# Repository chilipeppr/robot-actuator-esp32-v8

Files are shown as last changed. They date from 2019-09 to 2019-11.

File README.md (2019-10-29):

# robot-actuator-esp32-v8
This is the repo for the robot actuator v8 based on an ESP32 as the brains of each robot arm actuator.

This repository contains the latest design for the small actuator including:
- PCB schematic and board file (Eagle)
- Bill of Materials
- Fusion 360 files
- STL files for 3D printing
- NodeMCU ESP32 for Lua firmware with touch module, pulse counter module, RMT TX module, and gpiomatrix module.
- Lua code for actuator
- Link to ChiliPeppr http://chilipeppr.com/arm workspace to control the actuator and to ChiliPeppr ESP32 for Lua workspace for uploading code to the ESP32 device http://chilipeppr.com/esp32
- Heat management test results
- Youtube videos

This actuator is based on the amazing design of Jeff Kerr's (LoboCNC on Thingiverse) 3D printed robot arm WE-R2.4 six axis robot arm. https://www.thingiverse.com/thing:3327968

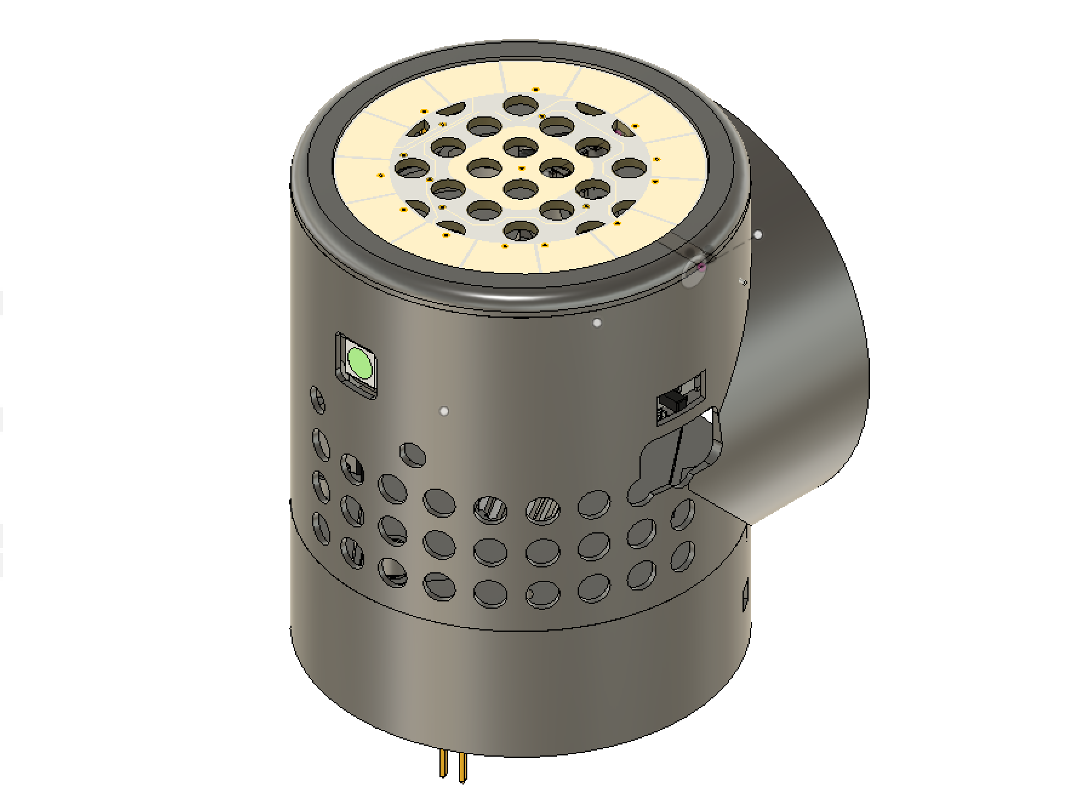
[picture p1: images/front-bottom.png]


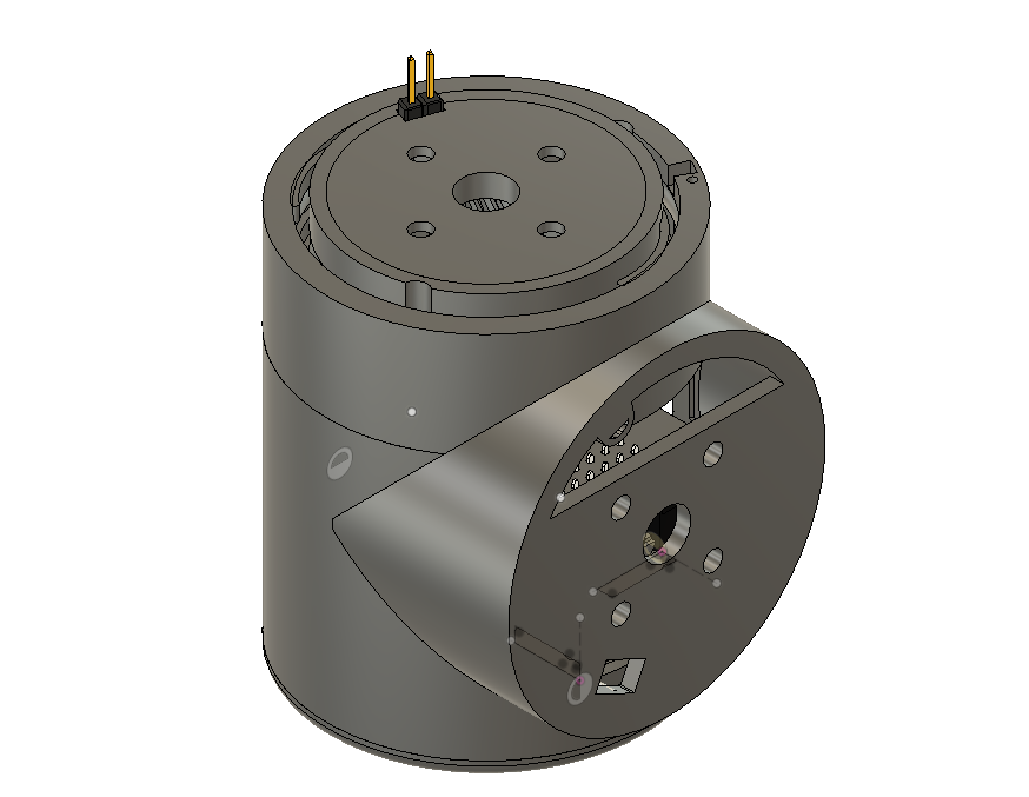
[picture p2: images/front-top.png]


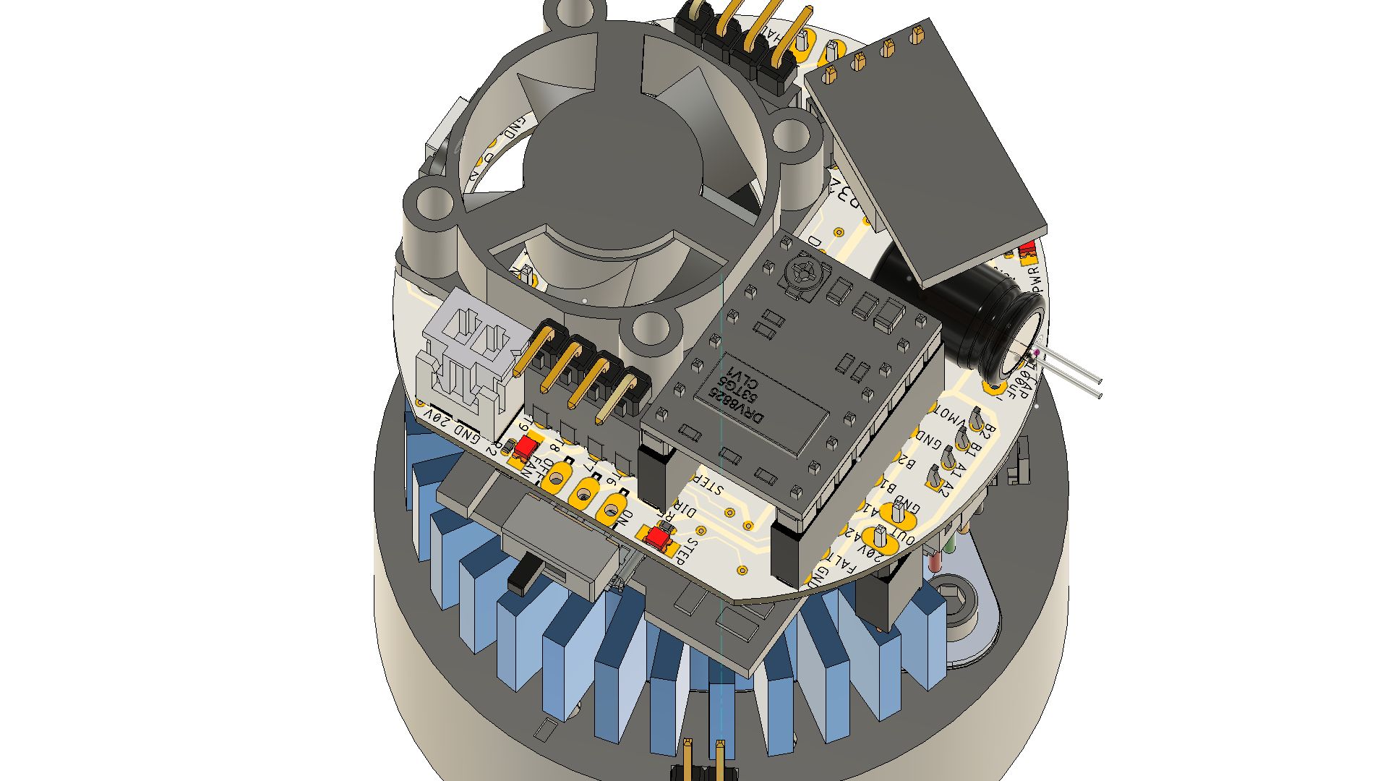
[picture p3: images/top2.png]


# Eagle Files

The main PCB board in Eagle.
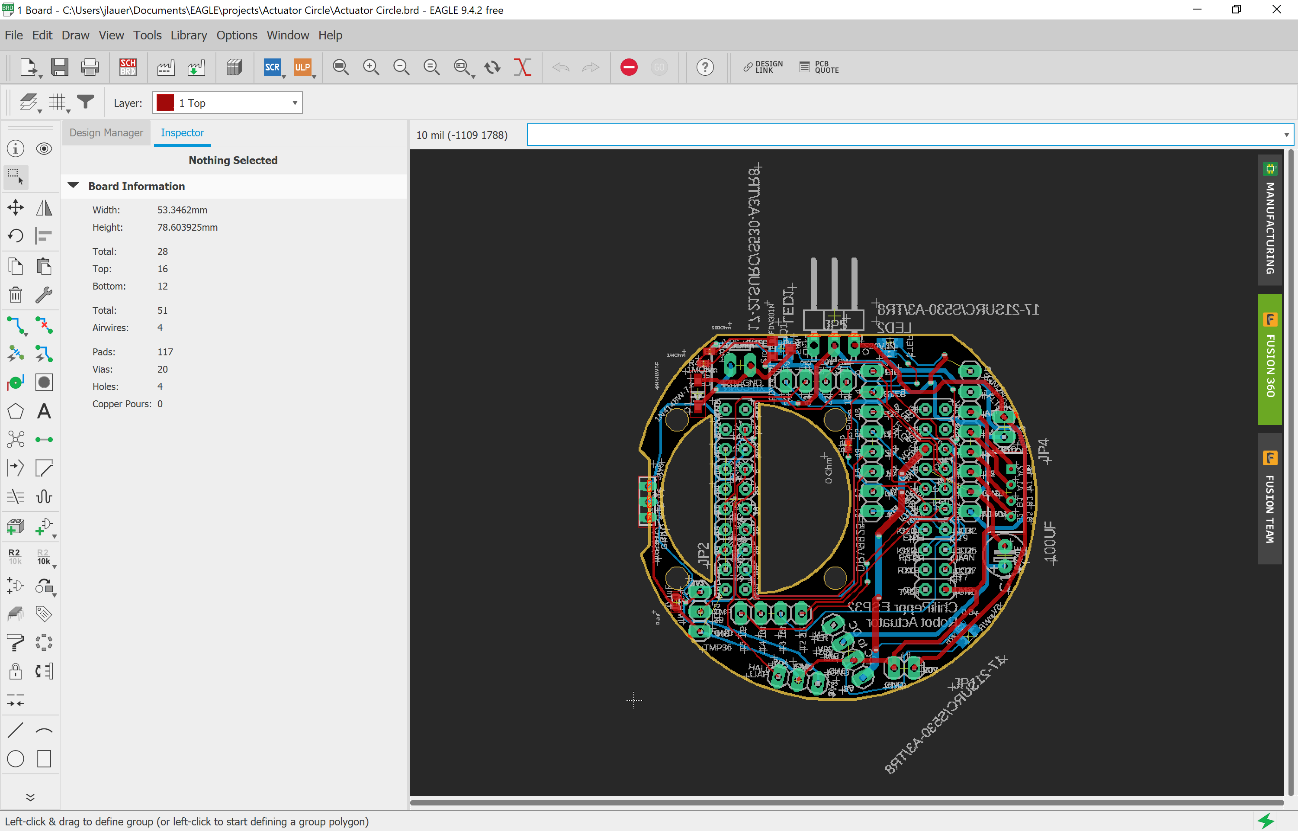
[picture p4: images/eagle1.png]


Top
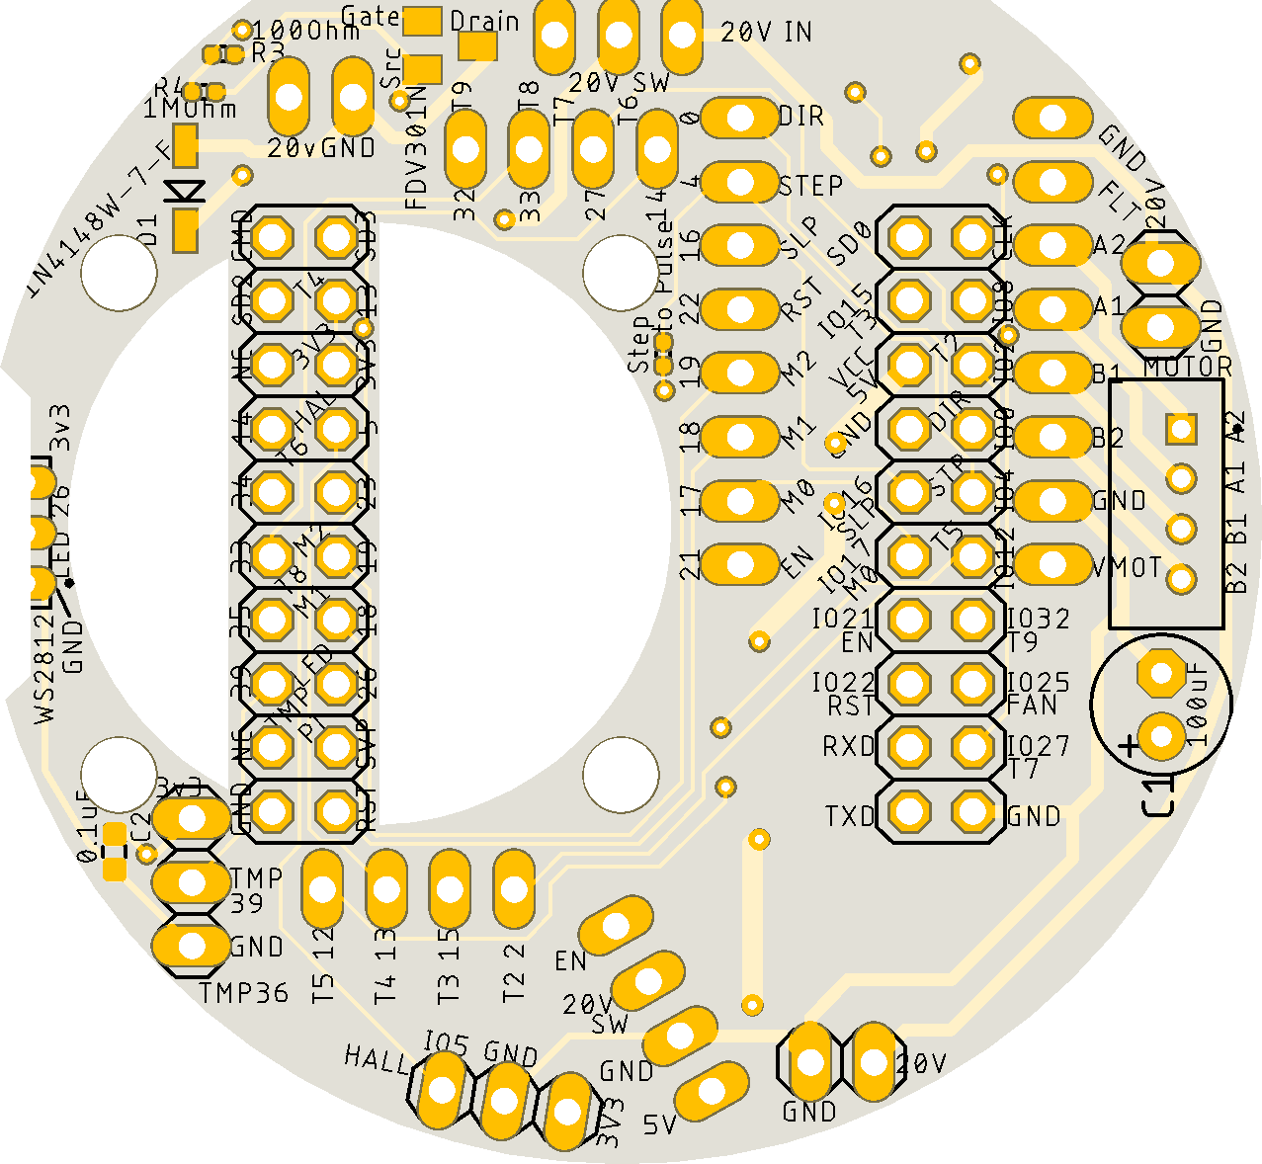
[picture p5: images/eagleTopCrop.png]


Bottom
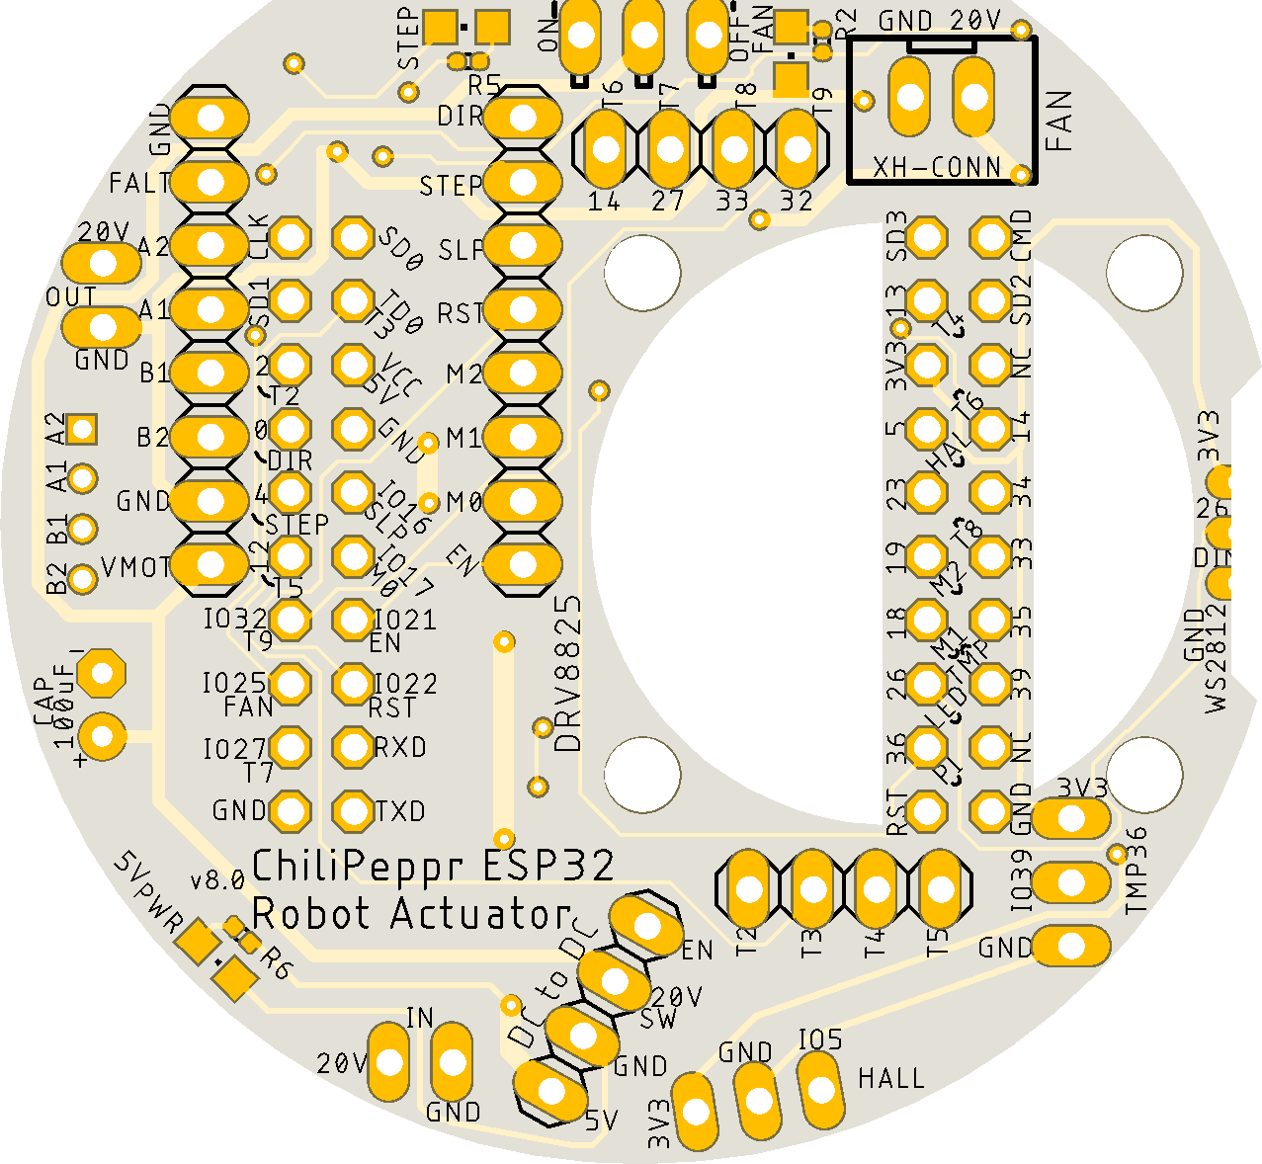
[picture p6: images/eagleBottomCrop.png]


The touch PCB board in Eagle.
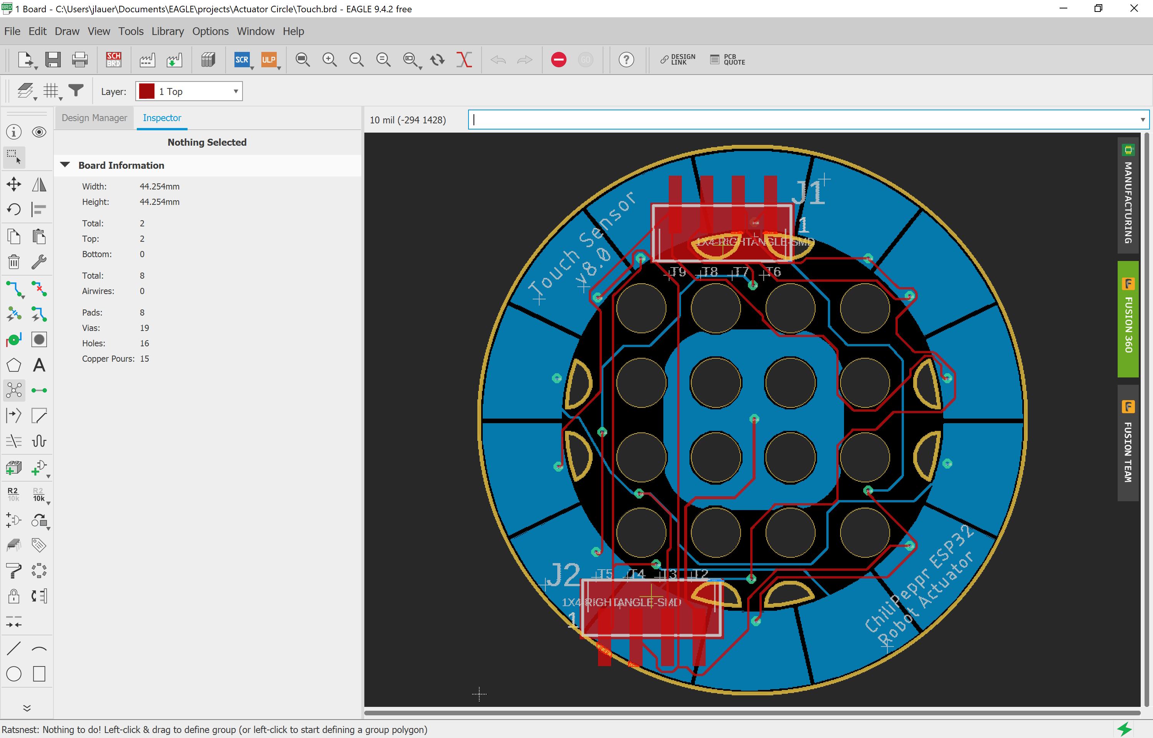
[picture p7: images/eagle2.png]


# Ordering PCBs

When ordering PCBs, keep in mind the thickness of the main PCB is 1.0 mm while the touch PCB is 1.2 mm. A white soldermask is recommended, but not important.

Main PCB is 1.0 mm thickness
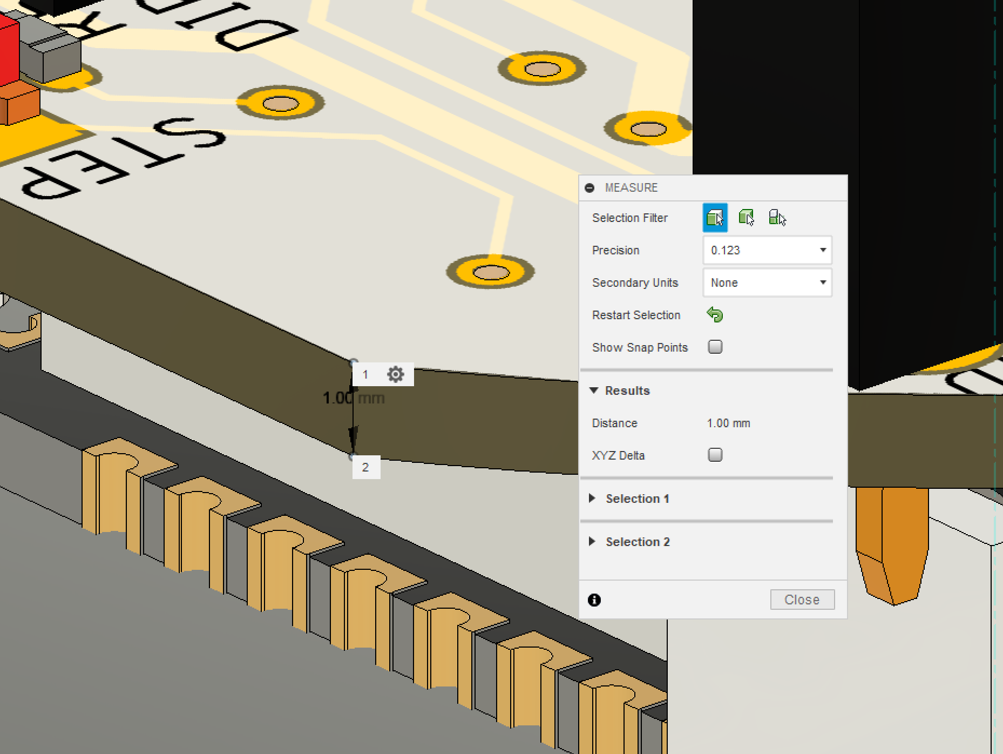
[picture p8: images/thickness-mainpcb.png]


Touch PCB is 1.2 mm thickness
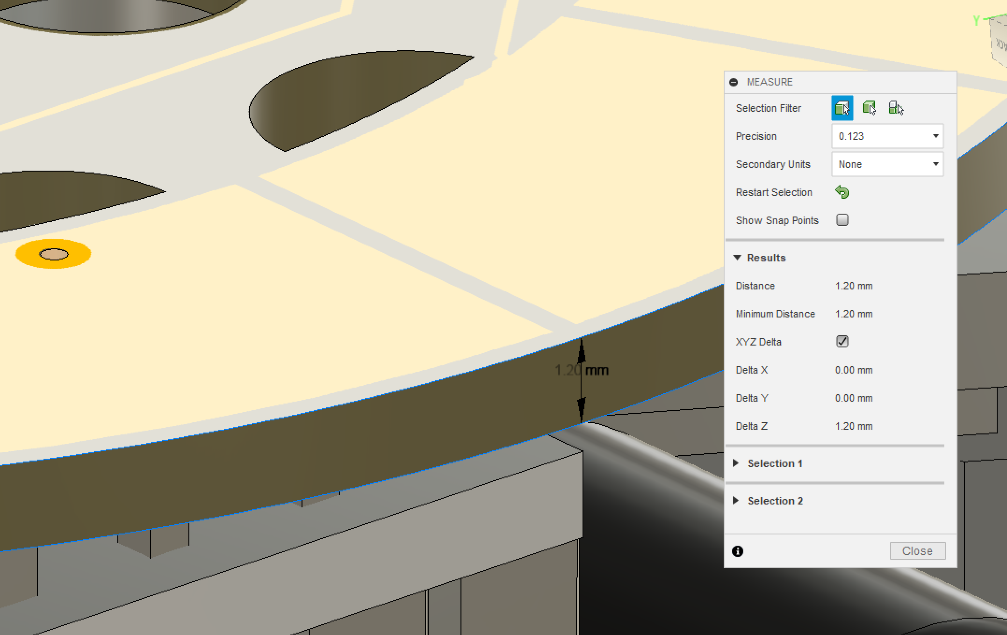
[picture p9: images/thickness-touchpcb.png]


# Fusion 360

The CAD files in Fusion360.
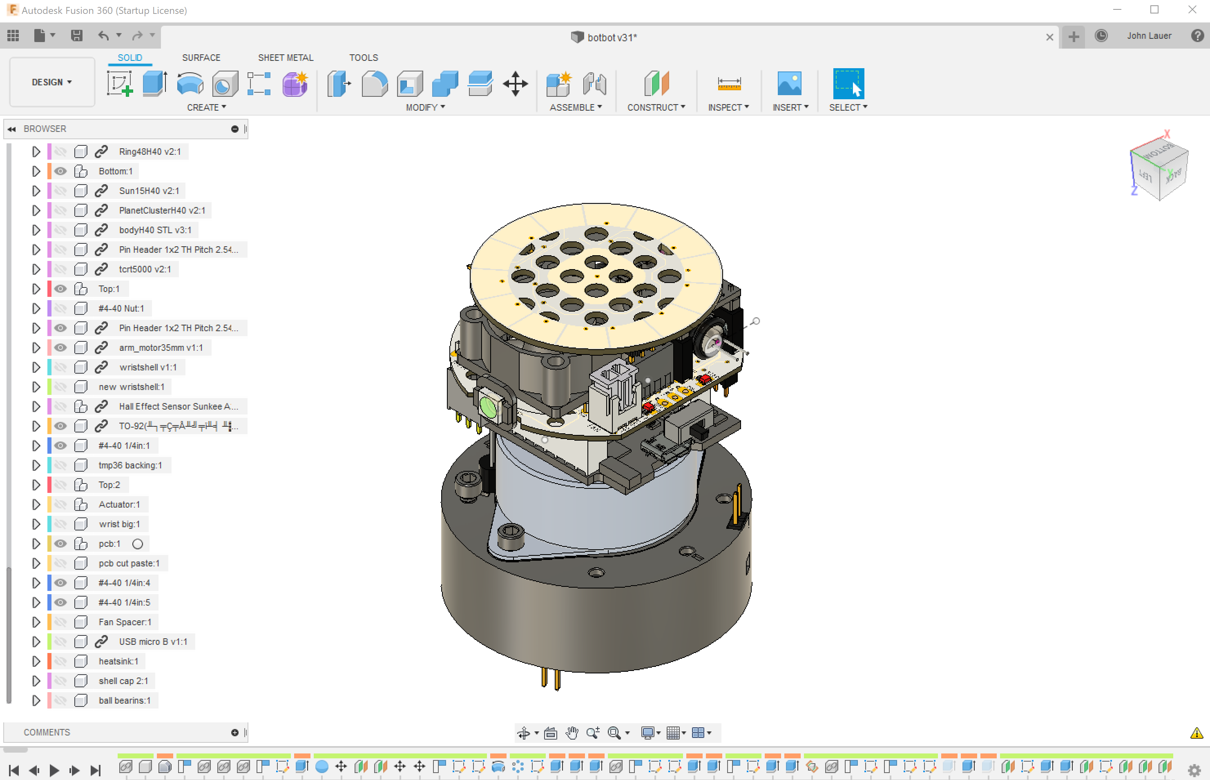
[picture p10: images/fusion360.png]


# ChiliPeppr

ChiliPeppr Robot Arm Workspace (Work in progress)
http://chilipeppr.com/arm

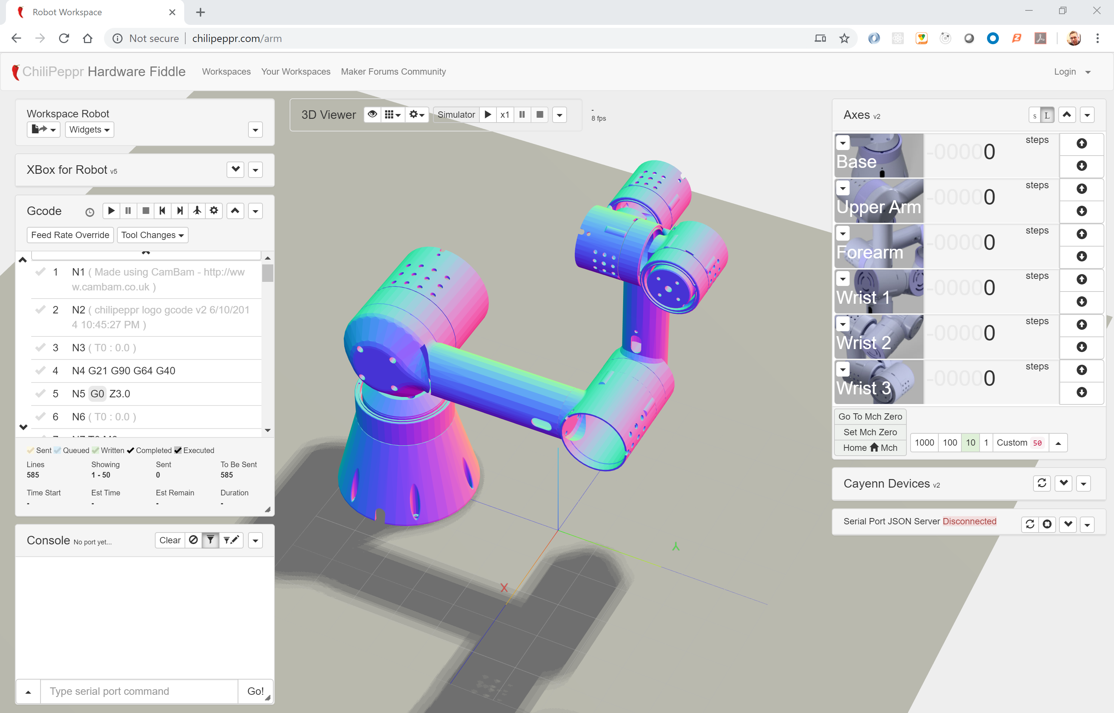
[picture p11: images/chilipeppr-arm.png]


ChiliPeppr ESP32 for Lua Workspace for editing/uploading code
http://chilipeppr.com/esp32

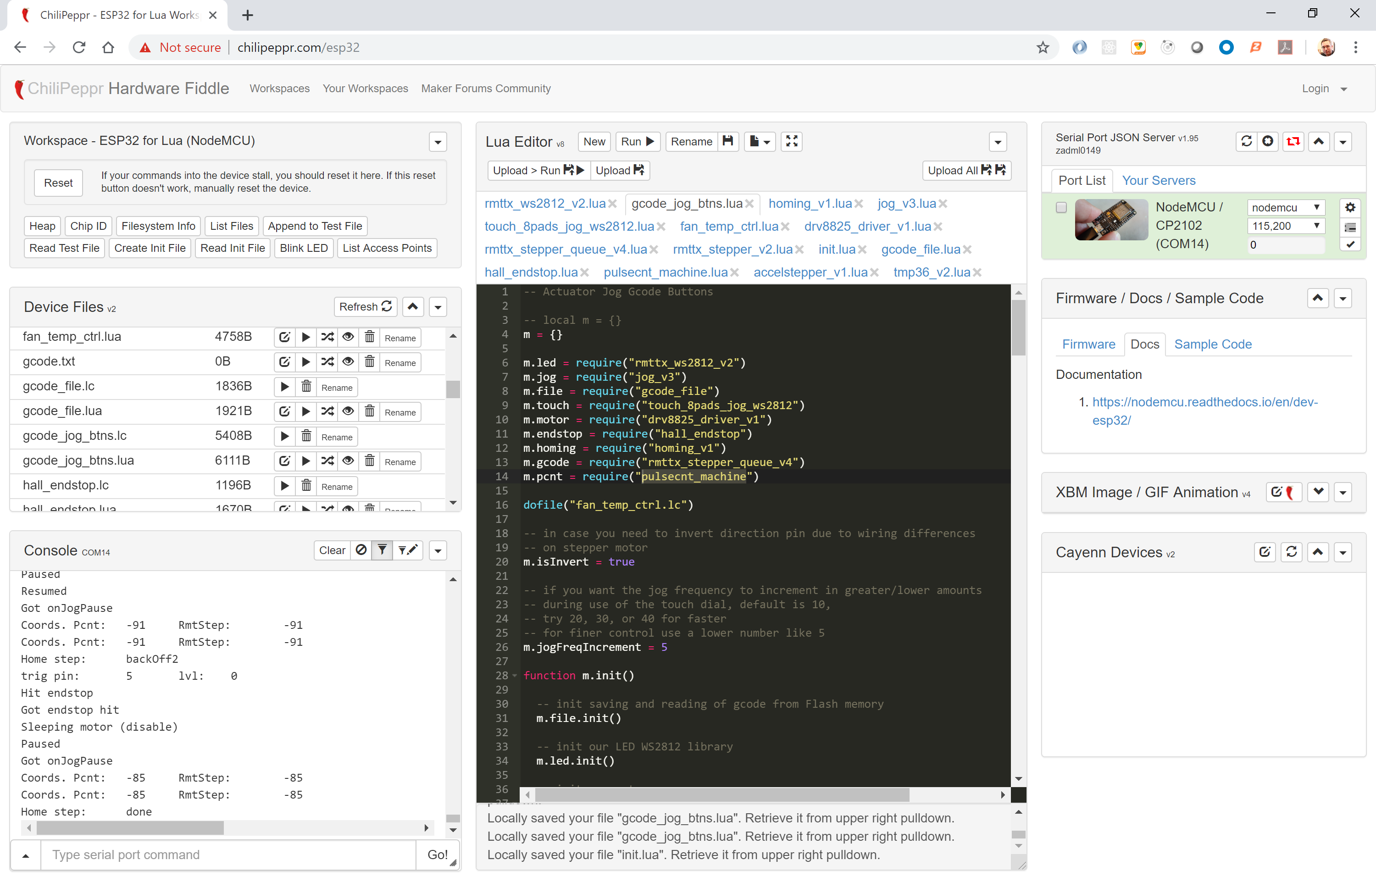
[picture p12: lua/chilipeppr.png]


# Heat Test

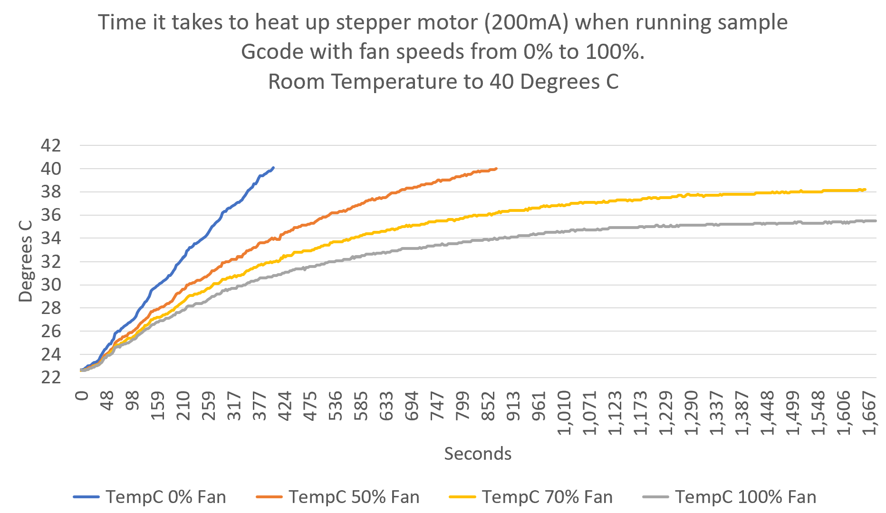
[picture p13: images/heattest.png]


# Youtube Videos

Part 1
https://www.youtube.com/watch?v=tEbJV32GyYU



Part 2
https://www.youtube.com/watch?v=RdmdFIhCo4M



Part 3
https://youtu.be/4o3d7_WZ_DQ



<!-- # Pins Used on ESP32

|GPIO|Used|Input|Output|Notes|
|----|-----|---|-----|
|0|Yes|Yes|Yes|motor.pinDir|
|1|TX pin|OK|debug output at boot|
|2|OK|OK|connected to on-board LED|
|3|OK|RX pin|HIGH at boot|
|4|OK|OK|
|5|OK|OK|outputs PWM signal at boot|
|6|x|x|connected to the integrated SPI flash|
|7|x|x|connected to the integrated SPI flash|
|8|x|x|connected to the integrated SPI flash|
|9|x|x|connected to the integrated SPI flash|
|10|x|x|connected to the integrated SPI flash|
|11|x|x|connected to the integrated SPI flash|
|12|OK|OK|boot fail if pulled high|
|13|OK|OK|
|14|OK|OK|outputs PWM signal at boot|
|15|OK|OK|outputs PWM signal at boot|
|16|OK|OK|
|17|OK|OK|
|18|OK|OK|
|19|OK|OK|
|21|OK|OK|
|22|OK|OK|
|23|OK|OK|
|25|OK|OK|
|26|OK|OK|
|27|OK|OK|
|32|OK|OK|
|33|OK|OK|
|34|OK|input only|
|35|OK|input only|
|36|OK|input only|
|39|OK|input only| -->

# Bill of Materials

| Ref | Part |  Price |  Quantity  |  Ext Price  | URL | Notes |
|---|---|---|---|---|---|---|
| | | | | | | |
| | PCB | | |  $- | | |
| | ESP32 Wemos Mini |  $4.05 |  1 |  $4.05 | https://www.aliexpress.com/item/32839344778.html | |
| | 2x10 Pin Header Female for ESP32 |  $0.12 |  2 |  $0.24 | https://lcsc.com/product-detail/Pin-Header-Female-Header_Boom-Precision-Elec-2-54mm-2-10-Straight-Female-header_C30867.html | Solder to the ESP32 board |
| C1 | 2x10 Pin Header Male for ESP32 |  $0.10 |  1 |  $0.10 | https://lcsc.com/product-detail/Pin-Header-Female-Header_Shenzhen-Cankemeng-Headers-Pins-2-10P-2-54mm-Straight-line_C124359.html | Solder to main PCB |
| | DRV8825 |  $0.88 |  1 |  $0.88 | https://www.aliexpress.com/item/33010878323.html | The most popular stepper driver out there. Simple and easy. |
| | 100uF 50V Capacitor for DRV8825 |  $0.13 |  1 |  $0.13 | https://lcsc.com/product-detail/Aluminum-Electrolytic-Capacitors-Leaded_PANASONIC-EEUFM1H101_C128473.html | The big capacitor for stepper motor driver |
| | DC to DC 24V to 5V Converter |  $0.48 |  1 |  $0.48 | https://www.aliexpress.com/item/32796268715.html | Little board from Aliexpress to get us to 5V on the cheap |
| | Fan 25mm 12V |  $1.08 |  1 |  $1.08 | https://www.aliexpress.com/item/33026177502.html | Silent fan that we overdrive to 20v for brief periods if heat spikes, otherwise we leave it off |
| R3 | Fan Mosfet FDV301N 25V 220mA SOT-23 |  $0.04 |  1 |  $0.04 | https://lcsc.com/product-detail/MOSFET_ON-Semicon_FDV301N_ON-Semicon-ON-FDV301N_C15310.html | Allows PWM speed control of fan. Run around 20Hz. |
| R4 | Fan Diode Protector 100V 300mA SOD-123 |  $0.02 |  1 |  $0.02 | https://lcsc.com/product-detail/Switching-Diode_DIODES_1N4148W-7-F_1N4148W-7-F_C83528.html | When fan switches off from Mosfet, it generates back current, so this diode lets it loop back into the fan to get absorbed |
| | Fan 100Ohm gate resistor 0402 |  $0.01 |  1 |  $0.01 | https://lcsc.com/product-detail/Chip-Resistor-Surface-Mount_100R-100R-1_C106232.html | Absorbs feedback attenuation |
| | Fan 1MOhm pull-down resistor 0402 |  $0.01 |  1 |  $0.01 | https://lcsc.com/product-detail/Chip-Resistor-Surface-Mount_1MR-105-5_C144054.html | Pulldown resistor to ground to shut off mosfet |
| | JST XH Male Connector for fan |  $0.04 |  1 |  $0.04 | https://lcsc.com/product-detail/Wire-To-Board-Wire-To-Wire-Connector_JST-Sales-America_B2B-XH-A-LF-SN_JST-Sales-America-B2B-XH-A-LF-SN_C158012.html | |
| | JST XH Crimp Connector for fan wire |  $0.01 |  2 |  $0.02 | https://lcsc.com/product-detail/New-Arrivals_JST-Sales-America-SXH-001T-P0-6N_C385122.html | In case you have to reterminate the fan wire, get these crimp connectors. You need a crimp tool. |
| | JST XH Female Connector for fan wire |  $0.02 |  1 |  $0.02 | https://lcsc.com/product-detail/Rectangular-Connectors-Housings_JST-Sales-America_XHP-2_JST-Sales-America-XHP-2_C144401.html | In case you have to reterminate the fan wire, get this female housing to slide the crimp connectors into |
| | WS2812B White |  $0.15 |  1 |  $0.15 | https://www.aliexpress.com/item/32960205936.html | Break off one LED and solder to side of PCB at 90 degree angle. Connect center pin to DIN, not DOUT. |
| | Red LED 0805 |  $0.02 |  3 |  $0.06 | https://lcsc.com/product-detail/Light-Emitting-Diodes-LED_0805-Red-LED-Iv-61mcd-Typ-atIF-20mA_C72037.html | Indicator LEDs |
| R5, R2 | 1KOhm current limit resistor for LED 0402 |  $0.01 |  2 |  $0.02 | https://lcsc.com/product-detail/Chip-Resistor-Surface-Mount_1KR-1001-1_C106235.html | The LEDs on the 3.3v bus for step and fan indicator use 1K to give LED about 1ma of current so it lights up very dim, but enough to indicate status. |
| R6 | 2KOhm current limit resistor for power LED 0402 |  $0.01 |  1 |  $0.01 | https://lcsc.com/product-detail/Chip-Resistor-Surface-Mount_Uniroyal-Elec-0402WGF2001TCE_C4109.html | The power LED is on a 5v bus. 2K gives it about 1.5ma of current for a dim indicator. |
| | 8 Pin Female Header 2.54mm |  $0.14 |  2 |  $0.28 | https://lcsc.com/product-detail/Pin-Header-Female-Header_Changjiang-Connectors-A2541HWV-8P_C225505.html | 2 needed for DRV8825 connection to main PCB. |
| | 4 Pin Female Header 2.54mm |  $0.07 |  3 |  $0.22 | https://lcsc.com/product-detail/Pin-Header-Female-Header_Shenzhen-Cankemeng-Female-header-1-4P-2-54mm-Straight-line_C124413.html | 1 for DC to DC, 2 for touch sensor PCB connection |
| | 3 Pin Female Header 2.54mm |  $0.06 |  2 |  $0.11 | https://lcsc.com/product-detail/Pin-Header-Female-Header_Shenzhen-Cankemeng-22025403P00CKMT_C146690.html | One for Hall sensor, one for TMP36. |
| | 2 Pin Female Header 2.54mm |  $0.03 |  4 |  $0.10 | https://lcsc.com/product-detail/Pin-Header-Female-Header_Boom-Precision-Elec-2-54-1-2PFemale_C49661.html | 2 for incoming 20v from slip ring. 2 for outgoing 20v to slip ring. |
| | JST PH B4B-K-S Male Header for Stepper |  $0.17 |  1 |  $0.17 | https://lcsc.com/product-detail/Wire-To-Board-Wire-To-Wire-Connector_JST-Sales-America_B4B-PH-K-LF-SN_JST-Sales-America-B4B-PH-K-LF-SN_C265289.html | Socket soldered to PCB |
| | JST PHR-4 Female Header for Stepper Cable |  $0.02 |  1 |  $0.02 | https://lcsc.com/product-detail/Connectors_JST_PHR-4_PHR-4-4P-pitch2-0mm-Plastic-shell_C111514.html | End of wire crimped connector |
| C2 | JST SPH Crimp Connector |  $0.01 |  4 |  $0.03 | https://lcsc.com/product-detail/Rectangular-Connectors-Contacts_JST_SPH-002T-P0-5S_SPH-002T-P0-5S-PH-T-PH-2-0_C111515.html | Individual crimp connectors. You'll need a crimping tool. |
| | Toggle Switch |  $0.12 |  1 |  $0.12 | https://lcsc.com/product-detail/Toggle-Switches_Korean-Hroparts-Elec-K3-1260D-L1_C92657.html | Toggle on/off the 20v to all components |
| | Pin Male Header Right Angle 2.54mm (40 pins breakaway) |  $0.44 |  2 |  $0.88 | https://www.digikey.com/product-detail/en/0022286043/WM22771-ND/3158673 | Right angle needed for touch sensor connection. Actually, I had to create my own right angle ones from straight ones to be long enough. They need to be about 10mm long from the touch PCB down to the pin headers, so buy the longest straight ones you can and bend them, then cut to size after you try to fit. Or, you can buy them from digikey.  |
| | Pin Male Header Straight 2.54mm (40 pins breakaway) |  $0.14 |  1 |  $0.14 | https://lcsc.com/product-detail/Pin-Header-Female-Header_Nextronics-Engineering-Z-211-4011-0021-001_C113597.html | Break off all headers for the numerous areas that need a male header pin. |
| | 0.1uF Capacitor smoothing for TMP36 |  $0.01 |  1 |  $0.01 | https://lcsc.com/product-detail/Others_Vishay-Intertech_VJ0402G104KXQCW1BC_Vishay-Intertech-VJ0402G104KXQCW1BC_C169292.html | TMP36 can give somewhat noisy temperature measurements. This cap on the input 3.3v on sensor can smooth out the output readings. You can operate without this cap since the software does multiple readings to average it. |
| | | | | | | |
| | Actuator | | |  $- | | |
| | Stepper Motor 35mm |  $2.90 |  1 |  $2.90 | https://www.aliexpress.com/item/2054451318.html | Cut off the PCB and resolder the 4 Pin silicone wire to the leads on the stepper. Make wire long enough you can connect to PCB while it's outside the actuator, around 4 to 6 inches. |
| | Neodymium Disc Mini Magnet 3x1.5mm |  $0.05 |  1 |  $0.05 | https://www.aliexpress.com/item/32949884024.html | Magnet needed to trigger hall effect sensor |
| | Hall Effect Sensor SIP-3 |  $0.14 |  1 |  $0.14 | https://lcsc.com/product-detail/Sensors_SK1816G-G03-K_C73293.html | Place into slot on bottom of 3D printed actuator, then place compression 3D printed backing to keep in place as close to magnet as you can. |
| | Heatsink 540/550 Motor |  $1.00 |  1 |  $1.00 | https://www.aliexpress.com/item/33004830927.html | Cut heatsink in half to service 2 actuators |
| | 4 Pin 30AWG Silicone Wire Ultra Flexible |  $0.24 |  1 |  $0.24 | https://www.aliexpress.com/item/32870367030.html | Use this wire to connect hall effect and TMP36 sensors to main PCB. Solder 3 wires to each sensor and then to 2.54mm standard 3 pin female headers. |
| | TMP36 Temperature Sensor TO-92 |  $1.08 |  1 |  $1.08 | https://lcsc.com/product-detail/Temperature-Sensors_ADI_TMP36GT9Z_TMP36GT9Z_C53490.html | Temperature sensor is pushed against stepper motor to watch motor temp as it can get hot and melt the 3D printed parts, ruining the actuator. |
| | | | |  $- | | |
| | |  $13.78  | |  $14.84 | | |
| | | | | | | |
| | | | | | | |
| | Other Stepper Motors | | | | | |
| | Higher end 35mm stepper Moon's |  $25.00  |  1 |  $25.00 | https://www.moonsindustries.com/p/35mm-permanent-magnet-stepper-motors/35pm048s8-08001-000004611120001819 | Not sure it's worth the money, but this motor is nice. I'm finding the cheaper motors are just about as good, but perhaps not as quiet or tight feeling as the Moon's. |
| | Another cheap 35mm that's really nice |  $3.00 |  1 |  $3.00 | https://www.aliexpress.com/item/32975464158.html | This is a very nice motor and cheap, but you have to grind off the gear on the 3mm shaft, which is painful. |

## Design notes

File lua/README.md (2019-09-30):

You can upload this Lua code via the ChiliPeppr workspace for ESP32 located at:
http://chilipeppr.com/esp32

To use this workspace you need to download and run Serial Port JSON Server. You can do this from the widget in the upper right corner which has links to the releases for Windows, Mac, Linux, and Raspberry Pi. Then connect to SPJS from your workspace via connecting to localhost or the IP address of the machine running SPJS. 

Once you've connected to SPJS, it will show you a list of serial ports. Connect to your ESP32. Now load all of the files into the editor and click "Upload All" to get the code on the Flash memory of your ESP32. This will take a bit to upload them, but you'll here a ding sound when they are done.

Here is a screenshot of what your workspace should look similar to.


Then you can restart your ESP32 and it should run init.lua to launch all of the code so you can use your actuator.

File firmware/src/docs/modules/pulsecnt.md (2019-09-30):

# Pulse Counter Module
| Since  | Origin / Contributor  | Maintainer  | Source  |
| :----- | :--- | :--- | :--- |
| 2019-04-07 | [ChiliPeppr](https://github.com/chilipeppr) | John Lauer | [pulsecnt.c](../../components/modules/pulsecnt.c)|

The pulsecnt library handles sophisticated and automatic pulse counting using the built-in hardware on ESP32.
The pulsecnt library gives you a means to not rely on GPIO triggers to do your pulse counting and instead offload the work to independent hardware. You gain the ability to count pulses up to 80Mhz (speed of APB clock).
You can get a callback to Lua when different counting thresholds are reached, or when upper or lower counting limits are hit. You can count pulses on all GPIO ports. There is also a way to provide
a control GPIO for ignoring or decrementing pulses when the control signal is high or low.

[Youtube video of examples using the pulsecnt](https://youtu.be/vk5QZnWdlAA) library including push button counting, stepper motor step counting, and hall effect sensor counting.

## pulsecnt.create()

Create the pulse counter object.

### Syntax
`pulsecnt.create(unit, callbackOnEvents)`

### Parameters
- `unit` Required. ESP32 has 0 thru 7 units to count pulses on.
- `callbackOnEvents` Optional. Your Lua method to call on event. myfunction(unit, isThr0, isThr1, isLLim, isHLim, isZero) will be called. Event will be PCNT_EVT_THRES_0 (Threshold 0 hit), PCNT_EVT_THRES_1 (Threshold 1 hit), PCNT_EVT_L_LIM (Minimum counter value), PCNT_EVT_H_LIM (Maximum counter value), or PCNT_EVT_ZERO (counter value zero event)
- `isDebug` Optional. Turn on extra logging by passing in true.

### Returns
`pulsecnt` object

### Example
```lua
-- Example Pulse Counter for 1 channel with polling of pulse count

pinPulseInput  = 2

llim = -32768
hlim = 32767

pcnt = pulsecnt.create(7) -- Use unit 7 (0-7 are allowed)

pcnt:chan0Config(
  pinPulseInput, --pulse_gpio_num
  pulsecnt.PCNT_PIN_NOT_USED, --ctrl_gpio_num If no control is desired specify PCNT_PIN_NOT_USED 
  pulsecnt.PCNT_COUNT_INC, --pos_mode PCNT positive edge count mode
  pulsecnt.PCNT_COUNT_DIS, --neg_mode PCNT negative edge count mode
  pulsecnt.PCNT_MODE_KEEP, --lctrl_mode Ctrl low PCNT_MODE_KEEP, PCNT_MODE_REVERSE, PCNT_MODE_DISABLE
  pulsecnt.PCNT_MODE_KEEP, --hctrl_mode Ctrl high PCNT_MODE_KEEP, PCNT_MODE_REVERSE, PCNT_MODE_DISABLE
  llim, --counter_l_lim [Range -32768 to 32767]
  hlim  --counter_h_lim [Range -32768 to 32767]
)

-- Clear counting
pcnt:clear()

-- Poll the pulse counter
print("Current pulse counter val:" .. pcnt:getCnt())
```

### Example
```lua
-- Example Pulse Counter for 1 channel with callback

pinPulseInput = 2
thr0 = 2 
thr1 = 4
llim = -6
hlim = 6 

-- Callback on pulsecnt events
function onPulseCnt(unit, isThr0, isThr1, isLLim, isHLim, isZero)

  print("unit:", unit, "isThr0:", isThr0, "isThr1:", isThr1)
  print("isLLim:", isLLim, "isHLim:", isHLim, "isZero:", isZero)
  
  -- Figure out what counter triggered this
  if isThr0 then print("thr0 "..thr0.." triggered event") end 
  if isThr1 then print("thr1 "..thr1.." triggered event") end 
  if isLLim then print("llim "..llim.." triggered event") end 
  if isHLim then print("hlim "..hlim.." triggered event") end 
  if isZero then print("zero 0 triggered event") end 

  -- Get current count
  print("Current pulse counter val:" .. pcnt:getCnt())
end

pcnt = pulsecnt.create(0, onPulseCnt) -- Use unit 0

pcnt:chan0Config(
  pinPulseInput, --pulse_gpio_num
  pulsecnt.PCNT_PIN_NOT_USED, --ctrl_gpio_num If no control is desired specify PCNT_PIN_NOT_USED 
  pulsecnt.PCNT_COUNT_INC, --pos_mode PCNT positive edge count mode PCNT_COUNT_DIS, PCNT_COUNT_INC, PCNT_COUNT_DEC
  pulsecnt.PCNT_COUNT_DIS, --neg_mode PCNT negative edge count mode PCNT_COUNT_DIS, PCNT_COUNT_INC, PCNT_COUNT_DEC
  pulsecnt.PCNT_MODE_KEEP, --lctrl_mode When Ctrl low PCNT_MODE_KEEP, PCNT_MODE_REVERSE, PCNT_MODE_DISABLE
  pulsecnt.PCNT_MODE_KEEP, --hctrl_mode When Ctrl high PCNT_MODE_KEEP, PCNT_MODE_REVERSE, PCNT_MODE_DISABLE
  llim, --counter_l_lim [Range -32768 to 32767]
  hlim  --counter_h_lim [Range -32768 to 32767]
)

-- Clear counting
pcnt:clear()

-- Set counter threshold for low and high
pcnt:setThres(thr0, thr1)

-- Get current pulse counter. Should be zero at start.
print("Current pulse counter val:" .. pcnt:getCnt())
```

### Example
```lua
-- Example Pulse Counter for 2 push buttons
-- Button 1 increments the counter (chan0)
-- Button 2 decrements the counter (chan1)
-- The pulsecnt filter is used to debounce

pinPulseInput  = 2
pinPulseInput2  = 25

thr0 = 2 
thr1 = 4
llim = -6
hlim = 6 

-- Example callback
function onPulseCnt(unit, isThr0, isThr1, isLLim, isHLim, isZero)
  
  print("unit:", unit, "isThr0:", isThr0, "isThr1:", isThr1)
  print("isLLim:", isLLim, "isHLim:", isHLim, "isZero:", isZero)

  -- Figure out what counter triggered this
  if isThr0 then print("thr0 "..thr0.." triggered event") end 
  if isThr1 then print("thr1 "..thr1.." triggered event") end 
  if isLLim then print("llim "..llim.." triggered event") end 
  if isHLim then print("hlim "..hlim.." triggered event") end 
  if isZero then print("zero 0 triggered event") end 

  -- Get current count
  print("Current pulse counter val:" .. pcnt:getCnt())
  
end

pcnt = pulsecnt.create(0, onPulseCnt) -- Use unit 0

-- Set clock cycles for filter. Any pulses lasting shorter than 
-- this will be ignored when the filter is enabled. So, pulse 
-- needs to be high or low for longer than this filter clock 
-- cycle. Clock is 80Mhz APB clock, so one cycle is 
-- 1000/80,000,000 = 0.0000125 ms. 1023 cycles = 0.0127875 ms
-- so not much of a debounce for manual push buttons.
pcnt:setFilter(1023)

-- Button 1
pcnt:chan0Config(
  pinPulseInput, --pulse_gpio_num
  pulsecnt.PCNT_PIN_NOT_USED, --ctrl_gpio_num If no control is desired specify PCNT_PIN_NOT_USED 
  pulsecnt.PCNT_COUNT_INC, --pos_mode PCNT positive edge count mode
  pulsecnt.PCNT_COUNT_DIS, --neg_mode PCNT negative edge count mode
  pulsecnt.PCNT_MODE_KEEP, --lctrl_mode
  pulsecnt.PCNT_MODE_KEEP, --hctrl_mode 
  llim, --counter_l_lim
  hlim  --counter_h_lim
)

-- Button 2
pcnt:chan1Config(
  pinPulseInput2, --pulse_gpio_num
  pulsecnt.PCNT_PIN_NOT_USED, --ctrl_gpio_num If no control is desired specify PCNT_PIN_NOT_USED 
  pulsecnt.PCNT_COUNT_INC, --pos_mode PCNT positive edge count mode
  pulsecnt.PCNT_COUNT_DIS, --neg_mode PCNT negative edge count mode
  pulsecnt.PCNT_MODE_REVERSE, --lctrl_mode
  pulsecnt.PCNT_MODE_KEEP, --hctrl_mode 
  llim, --counter_l_lim
  hlim  --counter_h_lim
)

-- Clear counting
pcnt:clear()

-- Set counter threshold for low and high
pcnt:setThres(thr0, thr1)

-- Buttons are now setup
```

## pulsecntObj:chan0Config()

Configure channel 0 of the pulse counter object you created from the create() method.

### Syntax
`pulsecntObj:chan0Config(pulse_gpio_num, ctrl_gpio_num, pos_mode, neg_mode, lctrl_mode, hctrl_mode, counter_l_lim, counter_h_lim)`

### Parameters
- `pulse_gpio_num` Required. Any GPIO pin can be used.
- `ctrl_gpio_num` Required (although you can specify pulsecnt.PIN_NOT_USED to ignore). Any GPIO pin can be used. If you are trying to use a pin you use as gpio.OUT in other parts of your code, you can instead configure the pin as gpio.IN_OUT and write high or low to it to achieve your gpio.OUT task while still enabling the pulse counter to successfully read the pin state. 
- `pos_mode` Required. Positive rising edge count mode, i.e. count the pulse when the rising edge occurs.
  -    pulsecnt.PCNT_COUNT_DIS = 0 Counter mode: Inhibit counter (counter value will not change in this condition). 
  -    pulsecnt.PCNT_COUNT_INC = 1 Counter mode: Increase counter value. 
  -    pulsecnt.PCNT_COUNT_DEC = 2 Counter mode: Decrease counter value.
- `neg_mode` Required. Negative falling edge count mode, i.e. count the pulse when the falling edge occurs.
  -    pulsecnt.PCNT_COUNT_DIS = 0 Counter mode: Inhibit counter (counter value will not change in this condition). 
  -    pulsecnt.PCNT_COUNT_INC = 1 Counter mode: Increase counter value. 
  -    pulsecnt.PCNT_COUNT_DEC = 2 Counter mode: Decrease counter value.
- `lctrl_mode` Required. When `ctrl_gpio_num` is low how should the counter be influenced.
  -    pulsecnt.PCNT_MODE_KEEP = 0 Control mode: will not change counter mode. 
  -    pulsecnt.PCNT_MODE_REVERSE = 1 Control mode: invert counter mode (increase -> decrease, decrease -> increase). 
  -    pulsecnt.PCNT_MODE_DISABLE = 2 Control mode: Inhibit counter (counter value will not change in this condition).
- `hctrl_mode` Required. When `ctrl_gpio_num` is high how should the counter be influenced.
  -    pulsecnt.PCNT_MODE_KEEP = 0 Control mode: will not change counter mode. 
  -    pulsecnt.PCNT_MODE_REVERSE = 1 Control mode: invert counter mode (increase -> decrease, decrease -> increase). 
  -    pulsecnt.PCNT_MODE_DISABLE = 2 Control mode: Inhibit counter (counter value will not change in this condition).
- `counter_l_lim` Required. Range -32768 to 32767. The lower limit counter. You get a callback at this count and the counter is reset to zero after this lower limit is hit.
- `counter_h_lim` Required. Range -32768 to 32767. The high limit counter. You get a callback at this count and the counter is reset to zero after this high limit is hit.

### Returns
`nil`

## pulsecntObj:chan1Config()

Configure channel 1 of the pulse counter object you created from the create() method.

### Syntax
`pulsecntObj:chan1Config(pulse_gpio_num, ctrl_gpio_num, pos_mode, neg_mode, lctrl_mode, hctrl_mode, counter_l_lim, counter_h_lim)`

### Parameters
- `pulse_gpio_num` Required. Any GPIO pin can be used.
- `ctrl_gpio_num` Required (although you can specify pulsecnt.PIN_NOT_USED to ignore). Any GPIO pin can be used. If you are trying to use a pin you use as gpio.OUT in other parts of your code, you can instead configure the pin as gpio.IN and toggle gpio.PULL_UP or gpio.PULL_DOWN to achieve your gpio.OUT task while still enabling the pulse counter to successfully read the pin state.
- `pos_mode` Required. Positive rising edge count mode, i.e. count the pulse when the rising edge occurs.
  -    pulsecnt.PCNT_COUNT_DIS = 0 Counter mode: Inhibit counter (counter value will not change in this condition). 
  -    pulsecnt.PCNT_COUNT_INC = 1 Counter mode: Increase counter value. 
  -    pulsecnt.PCNT_COUNT_DEC = 2 Counter mode: Decrease counter value.
- `neg_mode` Required. Negative falling edge count mode, i.e. count the pulse when the falling edge occurs.
  -    pulsecnt.PCNT_COUNT_DIS = 0 Counter mode: Inhibit counter (counter value will not change in this condition). 
  -    pulsecnt.PCNT_COUNT_INC = 1 Counter mode: Increase counter value. 
  -    pulsecnt.PCNT_COUNT_DEC = 2 Counter mode: Decrease counter value.
- `lctrl_mode` Required. When `ctrl_gpio_num` is low how should the counter be influenced.
  -    pulsecnt.PCNT_MODE_KEEP = 0 Control mode: will not change counter mode. 
  -    pulsecnt.PCNT_MODE_REVERSE = 1 Control mode: invert counter mode (increase -> decrease, decrease -> increase). 
  -    pulsecnt.PCNT_MODE_DISABLE = 2 Control mode: Inhibit counter (counter value will not change in this condition).
- `hctrl_mode` Required. When `ctrl_gpio_num` is high how should the counter be influenced.
  -    pulsecnt.PCNT_MODE_KEEP = 0 Control mode: will not change counter mode. 
  -    pulsecnt.PCNT_MODE_REVERSE = 1 Control mode: invert counter mode (increase -> decrease, decrease -> increase). 
  -    pulsecnt.PCNT_MODE_DISABLE = 2 Control mode: Inhibit counter (counter value will not change in this condition).
- `counter_l_lim` Required. Range -32768 to 32767. The lower limit counter. You get a callback at this count and the counter is reset to zero after this lower limit is hit.
- `counter_h_lim` Required. Range -32768 to 32767. The high limit counter. You get a callback at this count and the counter is reset to zero after this high limit is hit.

### Returns
`nil`

### Example
```lua
-- Button 1 increment counter
pcnt:chan0Config(
  pinPulseInput, --pulse_gpio_num
  pulsecnt.PCNT_PIN_NOT_USED, --ctrl_gpio_num If no control is desired specify PCNT_PIN_NOT_USED 
  pulsecnt.PCNT_COUNT_INC, --pos_mode PCNT positive edge count mode
  pulsecnt.PCNT_COUNT_DIS, --neg_mode PCNT negative edge count mode
  pulsecnt.PCNT_MODE_KEEP, --lctrl_mode
  pulsecnt.PCNT_MODE_KEEP, --hctrl_mode 
  llim, --counter_l_lim
  hlim  --counter_h_lim
)

-- Button 2 decrement counter
pcnt:chan1Config(
  pinPulseInput2, --pulse_gpio_num
  pulsecnt.PCNT_PIN_NOT_USED, --ctrl_gpio_num If no control is desired specify PCNT_PIN_NOT_USED 
  pulsecnt.PCNT_COUNT_INC, --pos_mode PCNT positive edge count mode
  pulsecnt.PCNT_COUNT_DIS, --neg_mode PCNT negative edge count mode
  pulsecnt.PCNT_MODE_REVERSE, --lctrl_mode
  pulsecnt.PCNT_MODE_KEEP, --hctrl_mode 
  llim, --counter_l_lim
  hlim  --counter_h_lim
)
```

## pulsecntObj:setThres()

Set the threshold values to establish watchpoints for getting callbacks on.

### Syntax
`pulsecntObj:setThres(thr0, thr1)`

### Parameters
- `thr0` Required. Threshold 0 value. Range -32768 to 32767. This is a watchpoint value to get a callback with isThr0 set to true on this count being reached. 
- `thr1` Required. Threshold 1 value. Range -32768 to 32767. This is a watchpoint value to get a callback with isThr1 set to true on this count being reached.

### Returns
`nil`

### Example
```lua
pcnt:setThres(-2000, 2000) -- get callbacks when counter is -2000 or 2000
```
```lua
pcnt:setThres(500, 10000) -- get callbacks when counter is 500 or 10000
```

## pulsecntObj:setFilter()

Set a filter to ignore pulses on the `pulse_gpio_num` pin and the `ctrl_gpio_num` to avoid short glitches. Any pulses lasting shorter than this will be ignored.

### Syntax
`pulsecntObj:setFilter(clkCycleCnt)`

### Parameters
- `clkCycleCnt` Required. 0 to 1023 allowd. Any pulses lasting shorter than this will be ignored. A pulse needs to be high or low for longer than this filter clock cycle. Clock is 80Mhz APB clock, so one cycle is 1000/80,000,000 = 0.0000125 ms. The longest value of 1023 cycles = 0.0127875 ms.

### Returns
`nil`

### Example
```lua
pcnt:setFilter(1023) -- set max filter clock cylce count to ignore pulses shorter than 12.7us
```

## pulsecntObj:clear()

Clear the counter. Sets it back to zero.

### Syntax
`pulsecntObj:clear()`

### Parameters
None

### Returns
`nil`

### Example
```lua
pcnt:clear() -- set counter back to zero
```

## pulsecntObj:getCnt()

Get the current pulse counter.

### Syntax
`pulsecntObj:getCnt()`

### Parameters
None

### Returns
`integer`

### Example
```lua
val = pcnt:getCnt() -- get counter
print("Pulse counter:", val)
```

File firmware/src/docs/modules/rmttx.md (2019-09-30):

# RMT TX (Remote Control Transmit) Module
| Since  | Origin / Contributor  | Maintainer  | Source  |
| :----- | :--- | :--- | :--- |
| 2019-09-01 | [ChiliPeppr](https://github.com/chilipeppr) | John Lauer | [rmttx.c](../../components/modules/rmttx.c)|

The RMT TX (Remote Control Transmit) module allows you to use ESP32's hardware signal generating system to create pulses with exact timing for use cases such as infrared LED signalling, LED blink patterns, WS2812/APA102 LED control, or even stepper motor step signal pulsing.

The hardware is capable of signal timing as low as 

For further information please refer to the ESP-IDF docs for the RMT system
https://docs.espressif.com/projects/esp-idf/en/latest/api-reference/peripherals/rmt.html

Click the YouTube video below for a tutorial on how to use this RMT TX library including sample code.

YouTube Touch Tutorial Walkthrough video (https://youtu.be/6BxNFh3GaRA)

### RMT Tick Item

To use this library, you will need to familiarize yourself with an RMT tick item. An RMT tick item consists of a `[duration0, level0, duration1, level1]` array item. You specify an array of these items to tell the RMT hardware how long each high or low pulse is.
| RMT Tick Item | Min Value | Max Value | Description |
| :--- | :--- | :--- | :--- |
| duration0 | 0 | 32767 | The duration in ticks of how long the signal is at level0. | 
| level0 | 0 (low) | 1 (high)  | Whether the signal is high or low at this time. | 
| duration1 | 0 | 32767 | The duration in ticks of how long the signal is at level1. | 
| level1 | 0 (low) | 1 (high)  | Whether the signal is high or low at this time. | 

### Clock Divider

You will need to pick a clock divider setting which will determine the best tick length for your application. A good clock divider will maximize the available RMT tick duration 15-bit (1 - 32767) value that is specified per high/low pulse. 

| Clock Divider | Clock <br/>Frequency Hz | ns Per Tick | μs Per Tick | ms Per Tick | ns Max | μs Max | ms Max |
| :--- | :--- | :--- | :--- | :--- | :----- | :----- | :--- |
| 1 (Min) | 80,000,000 | 12.5 | 0.0125 | 0.0000125 |
| 8 | 10,000,000 | 100 | 0.1 | 0.0001 |
| 10 | 8,000,000 | 125 | 0.125 | 0.000125 |
| 80 | 1,000,000 | 1000 | 1 | 0.001 |
| 100 | 800,000 | 1250 | 1.25 | 0.00125 |
| 160 | 500,000 | 2000 | 2 | 0.002 |
| 255 (Max) | 313,725 | 3187.5 | 3.1875 | 0.0031875 |

<!-- |               <td colspan=3>Tick Duration               <td colspan=3>Duration Max Per RMT Item <br/>(Set dur0 or dur1 = 32767) | -->

### Examples of Clock Dividers for Different Use Cases

WS2812 LED's expect a high/low pulse from 0.4μs (400ns) to 50μs. Thus a clock divider of 8 makes the most sense giving us a 100ns resolution per tick.

Stepper motors using a typical DRV8825 driver expect a minimum step pulse duration of 2μs high and 2μs low. Thus, the best tick length would be 1μs so a clock divider of 80 could be used. However, most steppers mechanically operate with 20Khz down to 100Hz signals 

### Example Lua Code

Example code showing how to configure 8 pads.
- Main run file [touch_8pads_showlist_test.lua](../../lua_examples/touch/touch_8pads_showlist_test.lua)
- Library [touch_8pads_showlist.lua](../../lua_examples/touch/touch_8pads_showlist.lua)

Example code showing how to use 5 touch pads to jog a stepper motor at different frequencies depending on which pad is touched:
- Main run file [touchjog_main.lua](../../lua_examples/touch/touchjog_main.lua)
- Library [touchjog_touch.lua](../../lua_examples/touch/touchjog_touch.lua)
- Library [touchjog_jog.lua](../../lua_examples/touch/touchjog_jog.lua)
- Library [touchjog_jog_drv8825.lua](../../lua_examples/touch/touchjog_jog_drv8825.lua)

## touch.create()

Create the touch sensor object. You must call this method first. Only one touch object may be created since most settings on the touch driver are global in nature such as threshold trigger mode, interrupt callbacks, and reference voltages.

### Syntax
```lua
tp = touch.create({
  pad = 0 || {0,1,2,3,4,5,6,7,8,9}, -- 0=GPIO4, 1=GPIO0, 2=GPIO2, 3=GPIO15, 4=GPIO13, 5=GPIO12, 6=GPIO14, 7=GPIO27, 8=GPIO33, 9=GPIO32
  cb = yourFunc, -- Callback on interrupt
  intrInitAtStart = true || false, -- Turn on/off interrupt at start.
  thres = 0..65536, -- All pads set to this thres. 
  thresTrigger = touch.TOUCH_TRIGGER_BELOW || touch.TOUCH_TRIGGER_ABOVE,
  filterMs = 0..4294967295 -- Filter is only available in polling mode. 
  lvolt = touch.TOUCH_LVOLT_0V4 || touch.TOUCH_LVOLT_0V5 || touch.TOUCH_LVOLT_0V6 || touch.TOUCH_LVOLT_0V7,
  hvolt = touch.TOUCH_HVOLT_2V4 || touch.TOUCH_HVOLT_2V5 || touch.TOUCH_HVOLT_2V6 || touch.TOUCH_HVOLT_2V7, 
  atten = touch.TOUCH_HVOLT_ATTEN_0V || touch.TOUCH_HVOLT_ATTEN_0V5 || touch.TOUCH_HVOLT_ATTEN_1V || touch.TOUCH_HVOLT_ATTEN_1V5 
  isDebug = true || false
})
```

### Parameters
List of values for configuration table:

- `pad` Required. padNum || {table of padNums}. Specify one pad like `pad = 4`, or provide a table list of pads. For example use `pad = {0,1,2,3,4,5,6,7,8,9}` to specify all pads. Pads allowed are 0=GPIO4, 1=GPIO0, 2=GPIO2, 3=GPIO15, 4=GPIO13, 5=GPIO12, 6=GPIO14, 7=GPIO27, 8=GPIO33, 9=GPIO32.
- `cb` Optional. Your Lua method that gets called on touch event. `myfunction(pads)` will be called where `pads` is a table of pads that were touched. The key is the pad number while the value is true, i.e. `pads = {[2]=true, [3]=true}` if pad 2 and 3 were both touched at the same time. When you specify a callback, interrupt mode is automatically turned on. You can specify `intrInitAtState = false` to manually turn on the interrupt later. If no callback is provided or nil is specified, then polling mode is active where you must call `tp:read()` to get the touch pad values.
- `intrInitAtStart` Optional. Defaults to true. Turn on interrupt at start. Set to false to if you want to configure the touch sensors first and then manually turn on interrupts later with `tp:intrEnable()`.
- `thres` Optional. Defaults to 0. Range is 0 to 65536. Provide a threshold value to be set on all pads specified in the `pad` parameter. Typically you will set thresholds per pad since pad size/shape/wire legnth influences the counter value per pad and thus your threshold is usually differnt per pad. You can set thres later per pad with `tp:setThres(padNum, thres)`.
- `thresTrigger` Optional. Defaults to touch.TOUCH_TRIGGER_BELOW.
  - touch.TOUCH_TRIGGER_BELOW
  - touch.TOUCH_TRIGGER_ABOVE
- `filterMs` Optional. Range is 0 to 4294967295 milliseconds. Used in polling mode only (if you provide a callback polling mode is disabled). Will filter noise for this many ms to give more consistent counter results. When filterMs is specified you will receive a 2nd return value in the `raw, filter = tp:read()` call with the filtered values in a Lua table.
- `lvolt` Optional. Low reference voltage 
  - touch.TOUCH_LVOLT_0V4
  - touch.TOUCH_LVOLT_0V5
  - touch.TOUCH_LVOLT_0V6
  - touch.TOUCH_LVOLT_0V7 
- `hvolt` Optional. High reference voltage 
  - touch.TOUCH_HVOLT_2V4
  - touch.TOUCH_HVOLT_2V5
  - touch.TOUCH_HVOLT_2V6
  - touch.TOUCH_HVOLT_2V7
- `atten` Optional. High reference voltage attenuation 
  - touch.TOUCH_HVOLT_ATTEN_0V
  - touch.TOUCH_HVOLT_ATTEN_0V5
  - touch.TOUCH_HVOLT_ATTEN_1V
  - touch.TOUCH_HVOLT_ATTEN_1V5
- `isDebug` Optional. Defaults to false. Set to true to get debug information during development. The info returned while debug is on can be very helpful in understanding polling vs interrupts, configuration, and threshold settings. Set to false during production.

### Returns
`touch` object

### Example 1 - Polling
```lua
-- Touch sensor with 5 touch pads for polling counter state

tp = touch.create({
  pad = {0,1,2,3,4}, -- pad = 0 || {0,1,2,3,4,5,6,7,8,9} 0=GPIO4, 1=GPIO0, 2=GPIO2, 3=GPIO15, 4=GPIO13, 5=GPIO12, 6=GPIO14, 7=GPIO27, 8=GPIO33, 9=GPIO32
  lvolt = touch.TOUCH_LVOLT_0V5, -- Low ref voltage TOUCH_LVOLT_0V4, TOUCH_LVOLT_0V5, TOUCH_LVOLT_0V6, TOUCH_LVOLT_0V7 
  hvolt = touch.TOUCH_HVOLT_2V7, -- High ref voltage TOUCH_HVOLT_2V4, TOUCH_HVOLT_2V5, TOUCH_HVOLT_2V6, TOUCH_HVOLT_2V7
  atten = touch.TOUCH_HVOLT_ATTEN_1V, -- High ref attenuation TOUCH_HVOLT_ATTEN_0V, TOUCH_HVOLT_ATTEN_0V5, TOUCH_HVOLT_ATTEN_1V, TOUCH_HVOLT_ATTEN_1V5 
  isDebug = true
})

function read()
  raw = tp:read()
  print("Pad", "RawVal")
  for key, value in pairs(raw) do
    print(key, value)
  end
end

read()
```

### Example 2 - Polling with Filtering
```lua
-- Touch sensor with 3 touch pads for polling with filtering

tp = touch.create({
  pad = {4,5,6}, -- pad = 0 || {0,1,2,3,4,5,6,7,8,9} 0=GPIO4, 1=GPIO0, 2=GPIO2, 3=GPIO15, 4=GPIO13, 5=GPIO12, 6=GPIO14, 7=GPIO27, 8=GPIO33, 9=GPIO32
  filterMs = 20, -- Polling mode only. Will filter noise for this many ms to give more consistent counter.
  lvolt = touch.TOUCH_LVOLT_0V5, -- Low ref voltage TOUCH_LVOLT_0V4, TOUCH_LVOLT_0V5, TOUCH_LVOLT_0V6, TOUCH_LVOLT_0V7 
  hvolt = touch.TOUCH_HVOLT_2V7, -- High ref voltage TOUCH_HVOLT_2V4, TOUCH_HVOLT_2V5, TOUCH_HVOLT_2V6, TOUCH_HVOLT_2V7
  atten = touch.TOUCH_HVOLT_ATTEN_1V, -- High ref attenuation TOUCH_HVOLT_ATTEN_0V, TOUCH_HVOLT_ATTEN_0V5, TOUCH_HVOLT_ATTEN_1V, TOUCH_HVOLT_ATTEN_1V5 
  isDebug = true
})

-- You will get 2 parameters from tp:read() when filterMs is specified in create()
function read()
  raw, filter = tp:read()
  -- Use sjson to make pretty output
  print("Touch raw:", sjson.encode(raw))
  print("Touch filt:", sjson.encode(filter))
end

-- Filtered vals will be similar to raw vals on first read.
read()
-- Read a second later to see how filtered vals are more stable.
tmr.create():alarm(1000, tmr.ALARM_SINGLE, read)
```

### Example 3 - Interrupt Touch / Untouch
```lua
-- Touch sensor with 1 pad for touch / untouch using threshold trigger mode
-- Swap TOUCH_TRIGGER_BELOW / TOUCH_TRIGGER_ABOVE on each callback
-- NOTE: Can only use this technique with 1 pad

pad = 6 -- 6=GPIO14

padState = 0 -- 0 means untouched
tp = nil -- Holds our touch sensor object

function onTouch(pads)
    
  if padState == 0 then
    -- we just got touched
    -- swap trigger mode to TOUCH_TRIGGER_ABOVE so we get interrupt
    -- on untouch
    padState = 1
    tp:setTriggerMode(touch.TOUCH_TRIGGER_ABOVE)
    print("Touch")
  else
    -- we just got untouched
    -- swap trigger mode to TOUCH_TRIGGER_BELOW so we get interrupt
    -- on touch
    padState = 0
    tp:setTriggerMode(touch.TOUCH_TRIGGER_BELOW)
    print("Untouch")
  end
  
end

function init()
  tp = touch.create({
    pad = pad, -- pad = 0 || {0,1,2,3,4,5,6,7,8,9} 0=GPIO4, 1=GPIO0, 2=GPIO2, 3=GPIO15, 4=GPIO13, 5=GPIO12, 6=GPIO14, 7=GPIO27, 8=GPIO33, 9=GPIO32
    cb = onTouch, -- Callback will get Lua table of pads/bool(true) that were touched.
    intrInitAtStart = false, -- Turn on interrupt at start. Default to true. Set to false to config first. Turn on later with tp:intrEnable()
    thresTrigger = touch.TOUCH_TRIGGER_BELOW, -- TOUCH_TRIGGER_BELOW or TOUCH_TRIGGER_ABOVE. Touch interrupt happens if ctr value is below or above.  
    lvolt = touch.TOUCH_LVOLT_0V5, -- Low ref voltage TOUCH_LVOLT_0V4, TOUCH_LVOLT_0V5, TOUCH_LVOLT_0V6, TOUCH_LVOLT_0V7 
    hvolt = touch.TOUCH_HVOLT_2V7, -- High ref voltage TOUCH_HVOLT_2V4, TOUCH_HVOLT_2V5, TOUCH_HVOLT_2V6, TOUCH_HVOLT_2V7
    atten = touch.TOUCH_HVOLT_ATTEN_1V, -- High ref attenuation TOUCH_HVOLT_ATTEN_0V, TOUCH_HVOLT_ATTEN_0V5, TOUCH_HVOLT_ATTEN_1V, TOUCH_HVOLT_ATTEN_1V5 
    isDebug = true
  })
  
end

function read()
  local raw = tp:read()
  print("Pad", "Val")
  for key,value in pairs(raw) do 
    print(key,value) 
  end
end

-- Do not touch during config
function config()
  local raw = tp:read()
  -- set threshold to 20% of baseline read state
  local thres = raw[pad] - math.floor(raw[pad] * 0.2)
  tp:setThres(pad, thres)
  print("Pad is at " .. raw[pad] .. " when not touched")
  print("Will trigger at thres: " .. thres)
  tp:intrEnable()
end

init()
read()
config()
```

### Example 4 - Interrupt Touch / Untouch with Timer
```lua
-- Touch sensor with 1 pad for touch / untouch using timer
-- Shows how to detect a touch and then an untouch

m = {}

m.pad = {8} -- 8=GPIO33

m._tp = nil -- will hold the touchpad obj
m._padState = 0 -- 0 means untouched
m._tmr = nil -- will hold the tmr obj
m._tmrWait = 50 -- ms to wait for no callback to indicate untouch

-- We will get a callback every 8ms or so when touched
-- We will reset the tmr each time and after 50ms will presume untouched event
function m.onTouch(pads)
  
  if m._padState == 0 then
    -- we just got touched
    m._padState = 1 -- 1 means touched
    m._tmr:start()
    print("Touch")
  else -- m._padState == 1
    -- we will get here on successive callbacks while touched
    -- we get them about every 8ms
    -- reset the tmr so it doesn't timeout yet
    m._tmr:stop()
    m._tmr:start()
  end
    
end

function m.onTmr()
  -- if we get the timer triggered, it means that we timed out
  -- from touch callbacks, so we presume the touch ended
  m._padState = 0
  print("Untouch")
end

function m.init()
  m._tp = touch.create({
    pad = m.pad, -- pad = 0 || {0,1,2,3,4,5,6,7,8,9} 0=GPIO4, 1=GPIO0, 2=GPIO2, 3=GPIO15, 4=GPIO13, 5=GPIO12, 6=GPIO14, 7=GPIO27, 8=GPIO33, 9=GPIO32
    cb = m.onTouch, -- Callback will get Lua table of pads/bool(true) that were touched.
    intrInitAtStart = false, -- Turn on interrupt at start. Default to true. Set to false in case you want to config first. Turn it on later with tp:intrEnable()
    thresTrigger = touch.TOUCH_TRIGGER_BELOW, -- TOUCH_TRIGGER_BELOW or TOUCH_TRIGGER_ABOVE. Touch interrupt will happen if counter value is below or above threshold.  
    lvolt = touch.TOUCH_LVOLT_0V5, -- Low ref voltage TOUCH_LVOLT_0V4, TOUCH_LVOLT_0V5, TOUCH_LVOLT_0V6, TOUCH_LVOLT_0V7 
    hvolt = touch.TOUCH_HVOLT_2V7, -- High ref voltage TOUCH_HVOLT_2V4, TOUCH_HVOLT_2V5, TOUCH_HVOLT_2V6, TOUCH_HVOLT_2V7
    atten = touch.TOUCH_HVOLT_ATTEN_1V, -- High ref attenuation TOUCH_HVOLT_ATTEN_0V, TOUCH_HVOLT_ATTEN_0V5, TOUCH_HVOLT_ATTEN_1V, TOUCH_HVOLT_ATTEN_1V5 
    isDebug = true
  })
  
  -- Setup the tmr for the callback process
  m._tmr = tmr.create()
  m._tmr:register(m._tmrWait, tmr.ALARM_SEMI, m.onTmr)
  
end

function m.read()
  local raw = m._tp:read()
  print("Pad", "Val")
  for key,value in pairs(raw) do 
    print(key,value) 
  end
end

-- Do not touch pad during config
function m.config()
  local raw = m._tp:read()
  -- set threshold to 20% of baseline read state
  local thres = raw[m.pad] - math.floor(raw[m.pad] * 0.2)
  m._tp:setThres(m.pad, thres)
  print("Pad is at ", raw[m.pad], " as baseline")
  print("Will trigger at thres: ", thres)
  m._tp:intrEnable()
end

m.init()
m.read()
m.config()
```

## touchObj:read()

Read the touch sensor counter values for all pads configured in `touch.create()` method.

### Syntax
`raw, filter = tp:read()`

### Parameters
None

### Returns
- `raw` Lua table of touch sensor counter values per pad
- `raw, filter` A 2nd Lua table of touch sensor filtered counter values per pad is returned if `filterMs` is specified during the touch.create() method.

### Example 1 - Raw
```lua
raw = tp:read()
print("Pad", "Val")
for key,value in pairs(raw) do 
  print(key,value) 
end
```

### Example 2 - Raw / Filter
```lua
-- You get a filter Lua table if you specified filterMs in touch.create()
raw, filter = tp:read()
print("Pad", "Raw", "Filt")
print("---", "---", "----")
for key,value in pairs(raw) do 
  print(key,value,filter[key]) 
end
```

## touchObj:setThres(padNum, thresVal)

Set touch sensor interrupt threshold per pad. The threshold only matters if you are in interrupt mode, which only activates if you specify a callback in the `touch.create()` configuration.

### Syntax
`tp:setThres(padNum, thresVal)`

### Parameters
- `padNum` Required. One pad number can be specified here. If you did multiple pads you must call this per pad.
- `thresVal` Required. The threshold value to set for the pad interrupt trigger. If you set touch.TOUCH_TRIGGER_BELOW then the interrupt occurs when the touch counter goes below this threshold value, or vice versa for touch.TOUCH_TRIGGER_ABOVE.

### Returns
`nil`

### Example 1
```lua
-- Set threshold for pad 2 where baseline counter is around 800 and 
-- when touched is around 200, so trigger at mid-point around 500
tp:setThres(2, 500)
```
### Example 2
```lua
-- Configure by reading baseline, then setting threshold to 30% below base
local raw = tp:read()
print("Pad", "Base", "Thres")
for key,value in pairs(raw) do 
  if key ~= nil then
    -- reduce by 30%
    local thres = raw[key] - math.floor(raw[key] * 0.3)
    tp:setThres(key, thres)
    print(key, value, thres) 
  end
end
-- Now enable interrupts since our thresholds are correct
tp:intrEnable()
```

## touchObj:setTriggerMode()

Set the trigger mode globally for all touch pads. The trigger mode only matters in interrupt mode where you can tell the hardware to give you an interrupt if the counter on the pad falls above or below the threshold you specify. 

### Syntax
`tp:setTriggerMode(mode)`

### Parameters
- `mode` Required. touch.TOUCH_TRIGGER_BELOW or touch.TOUCH_TRIGGER_ABOVE can be specified. If your pad's baseline counter value is around 600 when not touched, and sits around 300 when touched, then you would set your threshold around 450. If you set touch.TOUCH_TRIGGER_BELOW then when the counter drops to 300 it would fall BELOW the threshold of 450, thus triggering the interrupt. This process works in the reverse for touch.TOUCH_TRIGGER_ABOVE.

### Returns
`nil`

### Example 1
```lua
-- Trigger callback when pad counter goes above threshold value
tp:setTriggerMode(touch.TOUCH_TRIGGER_ABOVE)
-- Trigger callback when pad counter goes below threshold value
tp:setTriggerMode(touch.TOUCH_TRIGGER_BELOW)
```

### Example 2
```lua
-- Configure touch hardware to callback on TOUCH_TRIGGER_BELOW during touch.create()
-- Then on first callback swap to TOUCH_TRIGGER_ABOVE when detecting touch
-- Then will get 2nd callback on untouch due to mode change
-- This only works with 1 pad since trigger mode is global for all pads

padState = 0 -- Set start padState

function onTouch(pads)
    
  if padState == 0 then
    -- we just got touched
    -- swap trigger mode to TOUCH_TRIGGER_ABOVE so we get interrupt
    -- on untouch
    padState = 1
    tp:setTriggerMode(touch.TOUCH_TRIGGER_ABOVE)
    print("Got touch")
  else
    -- we just got untouched
    -- swap trigger mode to TOUCH_TRIGGER_BELOW so we get interrupt
    -- on touch
    padState = 0
    tp:setTriggerMode(touch.TOUCH_TRIGGER_BELOW)
    print("Got untouch")
  end

  print("Pads:", sjson.encode(pads))

end
```

## touchObj:intrEnable()

Enable interrupt on the touch sensor hardware. You can specify `intrInitAtStart=false` during `touch.create()` and thus you would want to call this method later on after configuring your pad thresholds.

### Syntax
`tp:intrEnable()`

### Parameters
None

### Returns
`nil`

### Example
```lua
tp:intrEnable() -- Enable interrupt
```

## touchObj:intrDisable()

Disable interrupt on the touch sensor hardware.

### Syntax
`tp:intrDisable()`

### Parameters
None

### Returns
`nil`

### Example
```lua
tp:intrDisable() -- Disable interrupt
```

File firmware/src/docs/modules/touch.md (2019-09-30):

# Touch Sensor Module
| Since  | Origin / Contributor  | Maintainer  | Source  |
| :----- | :--- | :--- | :--- |
| 2019-07-20 | [ChiliPeppr](https://github.com/chilipeppr) | John Lauer | [touch.c](../../components/modules/touch.c)|

The touch sensor module enables you to easily interact with ESP32's built-in 10 touch sensors. The touch pad sensing process is under the control of a hardware-implemented finite-state machine (FSM) which is initiated by software (polling mode) or a dedicated hardware timer (interrupt mode). By using the interrupt mode you can offload the sensing away from the main CPU. There are several examples in the docs below on how to implement your code.

For further information please refer to the ESP-IDF docs for Touch Sensor
https://docs.espressif.com/projects/esp-idf/en/latest/api-reference/peripherals/touch_pad.html

Click the YouTube video below for a tutorial on how to use this touch library including sample touch sensors, how to set your touch counter thresholds, and what the touch counters look like in the touched/untouched state of a sensor pad.

YouTube Touch Tutorial Walkthrough video (https://youtu.be/6BxNFh3GaRA)

The touch sensors are on the following GPIO pins

| Touch Pad Number | GPIO | | Touch Pad Number | GPIO | 
| :--- | :--- | -  | :--- | :--- |
| 0 | GPIO4 | | 5 | GPIO12 |
| 1 | GPIO0 | | 6 | GPIO14 |
| 2 | GPIO2 | | 7 | GPIO27 |
| 3 | GPIO15 | | 8 | GPIO33 |
| 4 | GPIO13 | | 9 | GPIO32 |

### Example Lua Code

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

## touch.create()

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

### Syntax
```lua
tp = touch.create({
  pad = 0 || {0,1,2,3,4,5,6,7,8,9}, -- 0=GPIO4, 1=GPIO0, 2=GPIO2, 3=GPIO15, 4=GPIO13, 5=GPIO12, 6=GPIO14, 7=GPIO27, 8=GPIO33, 9=GPIO32
  cb = yourFunc, -- Callback on interrupt
  intrInitAtStart = true || false, -- Turn on/off interrupt at start.
  thres = 0..65536, -- All pads set to this thres. 
  thresTrigger = touch.TOUCH_TRIGGER_BELOW || touch.TOUCH_TRIGGER_ABOVE,
  filterMs = 0..4294967295 -- Filter is only available in polling mode. 
  lvolt = touch.TOUCH_LVOLT_0V4 || touch.TOUCH_LVOLT_0V5 || touch.TOUCH_LVOLT_0V6 || touch.TOUCH_LVOLT_0V7,
  hvolt = touch.TOUCH_HVOLT_2V4 || touch.TOUCH_HVOLT_2V5 || touch.TOUCH_HVOLT_2V6 || touch.TOUCH_HVOLT_2V7, 
  atten = touch.TOUCH_HVOLT_ATTEN_0V || touch.TOUCH_HVOLT_ATTEN_0V5 || touch.TOUCH_HVOLT_ATTEN_1V || touch.TOUCH_HVOLT_ATTEN_1V5 
  isDebug = true || false
})
```

### Parameters
List of values for configuration table:

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

### Returns
`touch` object

### Example 1 - Polling
```lua
-- Touch sensor with 5 touch pads for polling counter state

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

read()
```

### Example 2 - Polling with Filtering
```lua
-- Touch sensor with 3 touch pads for polling with filtering

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

-- Filtered vals will be similar to raw vals on first read.
read()
-- Read a second later to see how filtered vals are more stable.
tmr.create():alarm(1000, tmr.ALARM_SINGLE, read)
```

### Example 3 - Interrupt Touch / Untouch
```lua
-- Touch sensor with 1 pad for touch / untouch using threshold trigger mode
-- Swap TOUCH_TRIGGER_BELOW / TOUCH_TRIGGER_ABOVE on each callback
-- NOTE: Can only use this technique with 1 pad

pad = 6 -- 6=GPIO14

padState = 0 -- 0 means untouched
tp = nil -- Holds our touch sensor object

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

init()
read()
config()
```

### Example 4 - Interrupt Touch / Untouch with Timer
```lua
-- Touch sensor with 1 pad for touch / untouch using timer
-- Shows how to detect a touch and then an untouch

m = {}

m.pad = {8} -- 8=GPIO33

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

m.init()
m.read()
m.config()
```

## touchObj:read()

Read the touch sensor counter values for all pads configured in `touch.create()` method.

### Syntax
`raw, filter = tp:read()`

### Parameters
None

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

### Example 1 - Raw
```lua
raw = tp:read()
print("Pad", "Val")
for key,value in pairs(raw) do 
  print(key,value) 
end
```

### Example 2 - Raw / Filter
```lua
-- You get a filter Lua table if you specified filterMs in touch.create()
raw, filter = tp:read()
print("Pad", "Raw", "Filt")
print("---", "---", "----")
for key,value in pairs(raw) do 
  print(key,value,filter[key]) 
end
```

## touchObj:setThres(padNum, thresVal)

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

### Syntax
`tp:setThres(padNum, thresVal)`

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

### Returns
`nil`

### Example 1
```lua
-- Set threshold for pad 2 where baseline counter is around 800 and 
-- when touched is around 200, so trigger at mid-point around 500
tp:setThres(2, 500)
```
### Example 2
```lua
-- Configure by reading baseline, then setting threshold to 30% below base
local raw = tp:read()
print("Pad", "Base", "Thres")
for key,value in pairs(raw) do 
  if key ~= nil then
    -- reduce by 30%
    local thres = raw[key] - math.floor(raw[key] * 0.3)
    tp:setThres(key, thres)
    print(key, value, thres) 
  end
end
-- Now enable interrupts since our thresholds are correct
tp:intrEnable()
```

## touchObj:setTriggerMode()

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

### Syntax
`tp:setTriggerMode(mode)`

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

### Returns
`nil`

### Example 1
```lua
-- Trigger callback when pad counter goes above threshold value
tp:setTriggerMode(touch.TOUCH_TRIGGER_ABOVE)
-- Trigger callback when pad counter goes below threshold value
tp:setTriggerMode(touch.TOUCH_TRIGGER_BELOW)
```

### Example 2
```lua
-- Configure touch hardware to callback on TOUCH_TRIGGER_BELOW during touch.create()
-- Then on first callback swap to TOUCH_TRIGGER_ABOVE when detecting touch
-- Then will get 2nd callback on untouch due to mode change
-- This only works with 1 pad since trigger mode is global for all pads

padState = 0 -- Set start padState

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

  print("Pads:", sjson.encode(pads))

end
```

## touchObj:intrEnable()

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

### Syntax
`tp:intrEnable()`

### Parameters
None

### Returns
`nil`

### Example
```lua
tp:intrEnable() -- Enable interrupt
```

## touchObj:intrDisable()

Disable interrupt on the touch sensor hardware.

### Syntax
`tp:intrDisable()`

### Parameters
None

### Returns
`nil`

### Example
```lua
tp:intrDisable() -- Disable interrupt
```

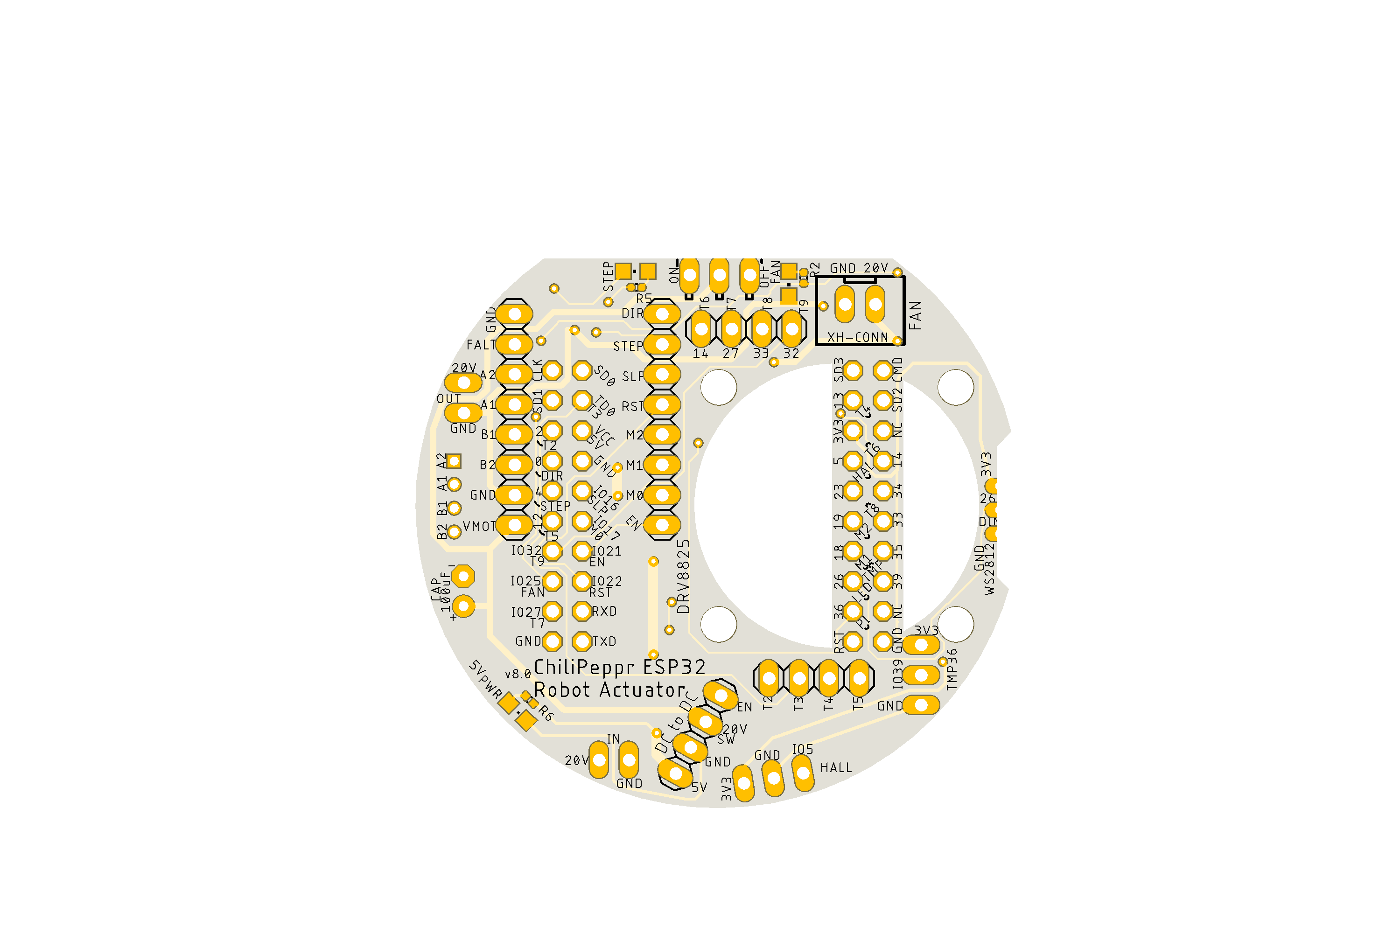
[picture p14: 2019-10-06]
images/eagleBottom.png

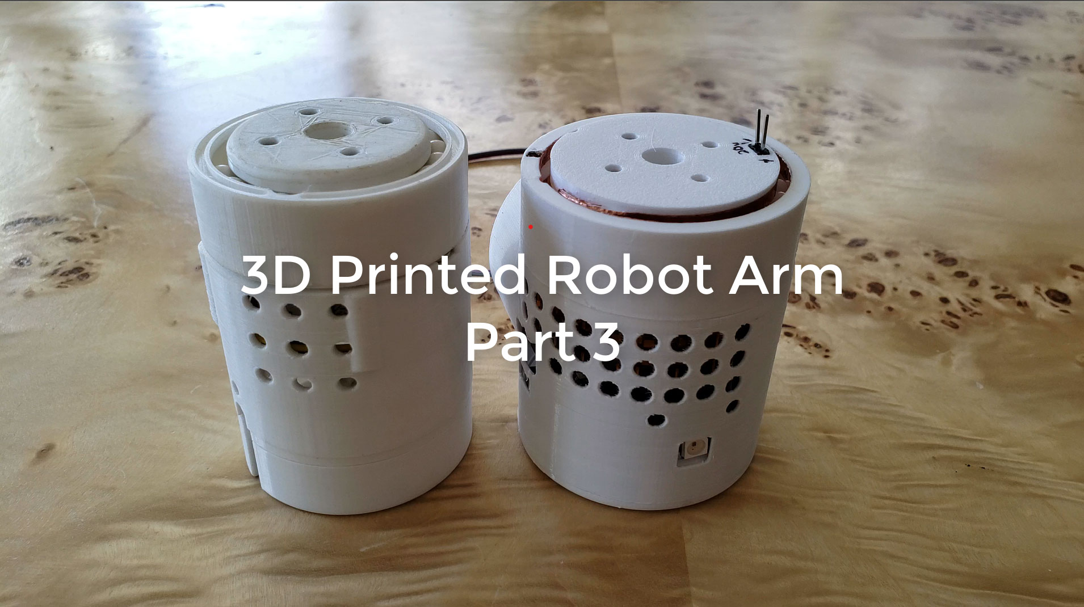
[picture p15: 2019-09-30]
images/youtube.jpg

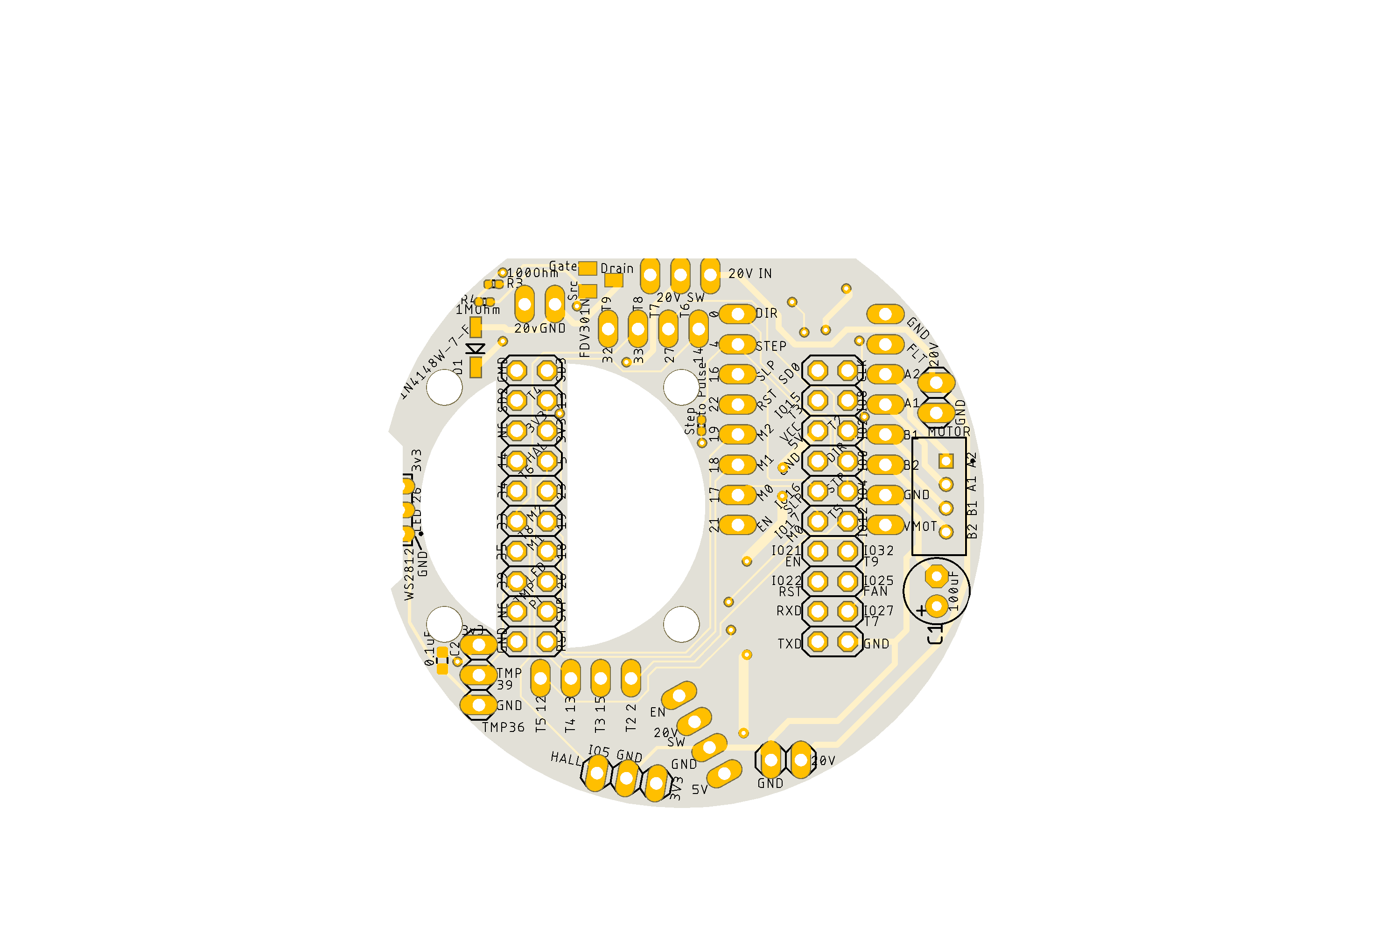
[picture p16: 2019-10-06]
images/eagleTop.png

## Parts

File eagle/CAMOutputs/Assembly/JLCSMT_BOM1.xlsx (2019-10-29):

Comment | Designator | Footprint | LCSC Part #（optional） | Alternate
NPN | Q1 | SOT23 | C20526 | C20526 | C20526
100Ω | R3 | 0402_R | C25076 | C22775
1MΩ | R4 | 0402_R | C26083 | C169373
1N4148W | D1 | SOD-123 | C81598 | C83528
100nF | C2 | 0603_C | C14663
Red | LED2 | 0805_LED | C84256

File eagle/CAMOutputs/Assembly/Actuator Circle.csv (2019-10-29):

Qty | Value | Device | Package | Parts | Description | AVAILABILITY | CREATED_BY | DESCRIPTION | DIGIKEY_PART_NUMBER | MANUFACTURER | MF | MP | MPN | PACKAGE | POPULARITY | PRICE | VALUE
2 |  | PINHD-1X2 | 1X02 | JP1, JP4 | PIN HEADER |  |  |  |  |  |  |  |  |  | 98
2 |  | PINHD-1X3 | 1X03 | HALL, TMP36 | PIN HEADER |  |  |  |  |  |  |  |  |  | 92
1 |  | PINHD-1X3/90 | 1X03/90 | JP5 | PIN HEADER |  |  |  |  |  |  |  |  |  | 17
3 |  | PINHD-1X4 | 1X04 | JP10, JP11, JP12 | PIN HEADER |  |  |  |  |  |  |  |  |  | 91
2 |  | PINHD-1X8 | 1X08 | JP8, JP9 | PIN HEADER |  |  |  |  |  |  |  |  |  | 67
2 |  | PINHD-2X10 | 2X10 | JP2, JP3 | PIN HEADER |  |  |  |  |  |  |  |  |  | 7
1 | 0 Ohm | RES-0402 | RES_0402 | R1 | RES SMD 0402 |  | ChiliPeppr |  |  |  |  |  |  | SMD 0402
1 | 0.1uf | CAP-0603-22UF-10V-MLCC | CAP_0603 | C2 | Multilayer Ceramic Capacitors MLCC - SMD/SMT 22uF 10V 0603 RoHS |  | ChiliPeppr |  | LCSC Part #: C86295 | Samsung Electro-Mechanics |  |  | CL10A226MP8NUNE | SMD 0603
1 | 100Ohm | RES-0402 | RES_0402 | R3 | RES SMD 0402 |  | ChiliPeppr |  |  |  |  |  |  | SMD 0402
1 | 100UF | CAPACITOR-PE2.5-6 | E2,5-6 | C1 | POLARIZED CAPACITOR, American symbol
3 | 17-21SURC/S530-A3/TR8 | LEDCHIPLED_0805 | CHIPLED_0805 | 5V, LED1, LED2 | LED
2 | 1K | RES-0402 | RES_0402 | R2, R5 | RES SMD 0402 |  | ChiliPeppr |  |  |  |  |  |  | SMD 0402
1 | 1MOhm | RES-0402 | RES_0402 | R4 | RES SMD 0402 |  | ChiliPeppr |  |  |  |  |  |  | SMD 0402
1 | 1N4148W-7-F | D-SOD123 | SOD123 | D1 | DIODE
1 | 2k | RES-0402 | RES_0402 | R6 | RES SMD 0402 |  | ChiliPeppr |  |  |  |  |  |  | SMD 0402
1 | B4B-PH-K-S(LF)(SN) | B4B-PH-K-S(LF)(SN) | JST_B4B-PH-K-S(LF)(SN) | MOTOR | PH Series 4 Position 2 mm Pitch Through Hole Crimp Top Entry Shrouded Header | Unavailable |  | PH Series 4 Position 2 mm Pitch Through Hole Crimp Top Entry Shrouded Header |  |  | JST Sales | B4B-PH-K-S_LF__SN_ |  | None |  | None
1 | FDV301N | SMD-MOSFET-N-CH-25V-220MA-FDV301N(SOT-23) | SOT23 | Q1 | FDV301N |  |  |  |  |  |  |  | FDV301N |  |  |  | FDV301N
1 | JST-XH-02-PIN-LONG-PAD | JST-XH-02-PIN-LONG-PAD | JST-XH-02-PACKAGE-LONG-PAD | XH-CONN | JST XH Connector 2 Pin
1 | PIN1X3-2MM | PIN1X3-2MM | PIN1X3-2MM | WS2812 | THT Vertical Pin Header WR-PHD, Pitch 2.00 mm, Single Row, 3 pins |  | PCBLayout.com |  |  | Würth Elektronik |  |  | 62000311121

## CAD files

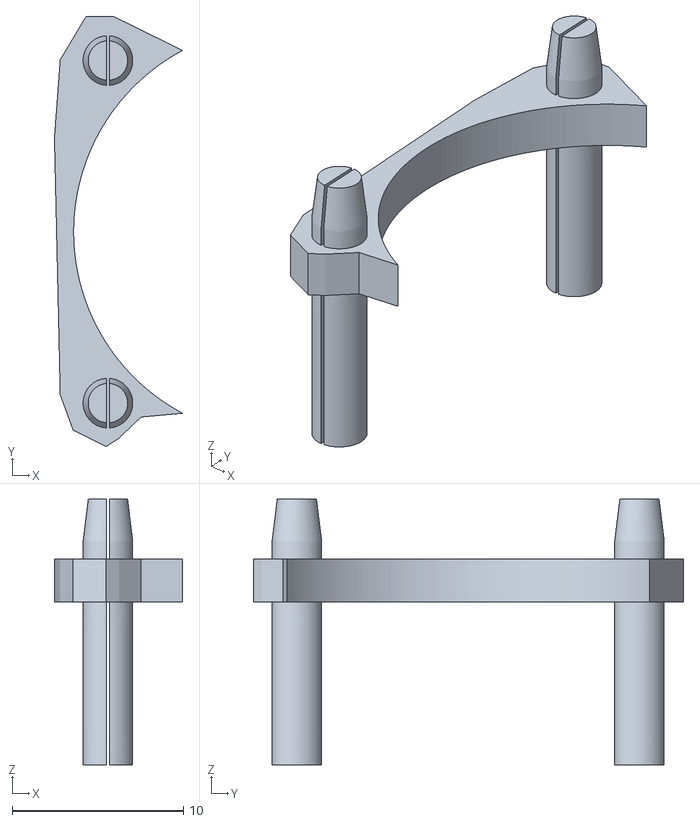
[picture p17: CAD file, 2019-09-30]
stl/fan spacer 6.stl
7.48 x 25.1 x 15.5

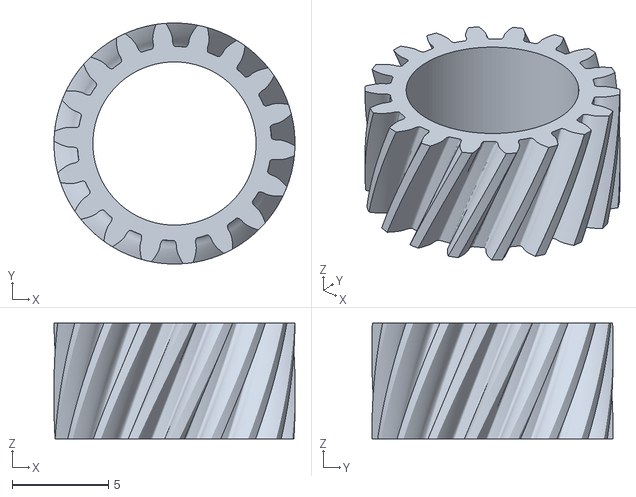
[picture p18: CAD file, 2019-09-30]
stl/Sun18H40.STL
12.5 x 12.5 x 6.00

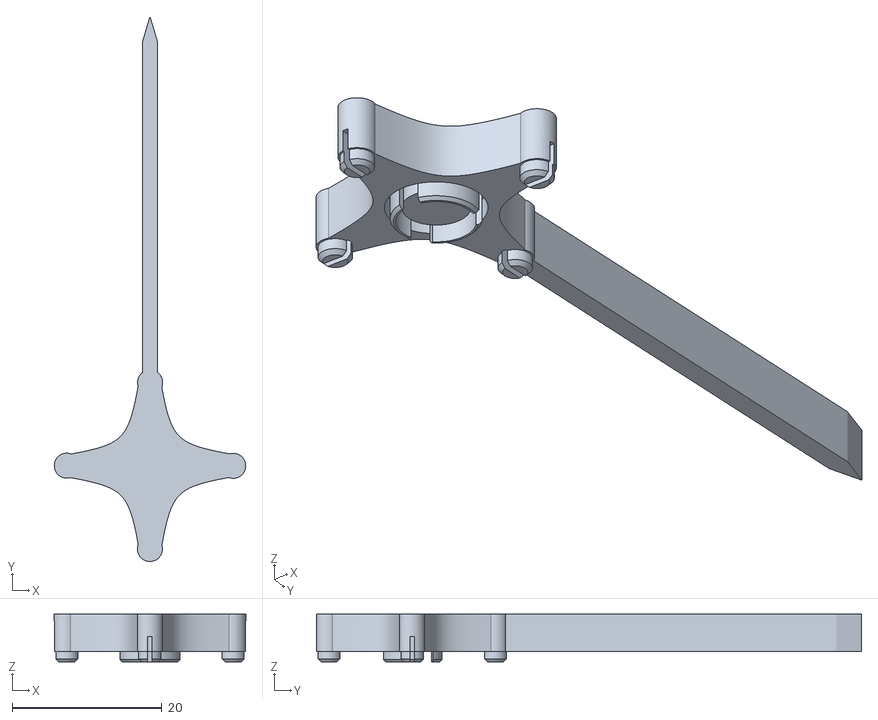
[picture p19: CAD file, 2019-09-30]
stl/test point 5.stl
25.6 x 72.8 x 6.40

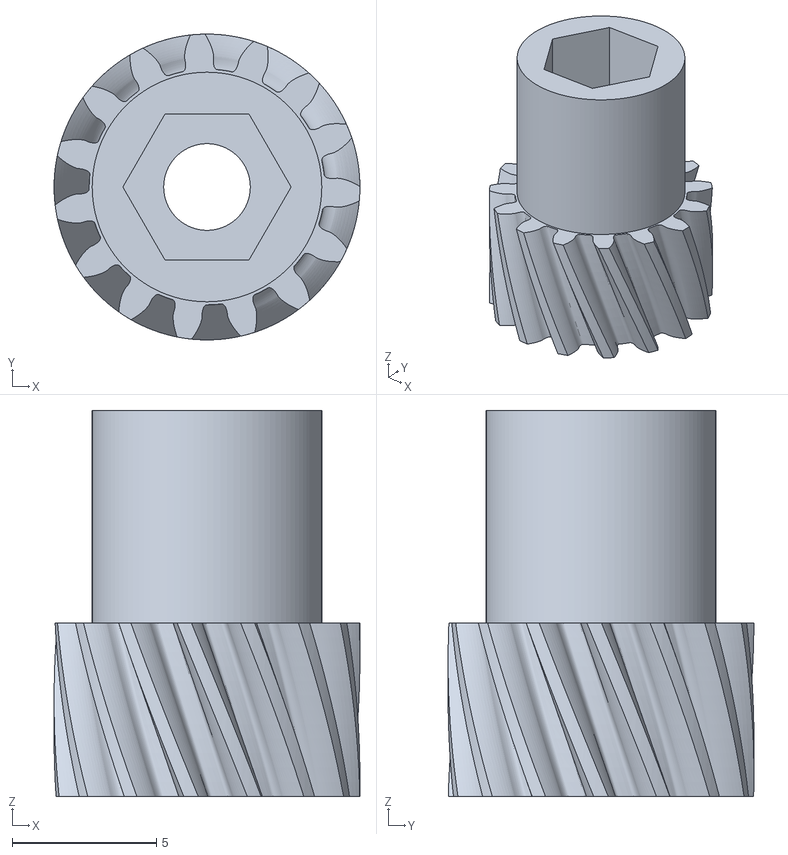
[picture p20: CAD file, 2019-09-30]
stl/Sun15H40.STL
10.6 x 10.6 x 13.4

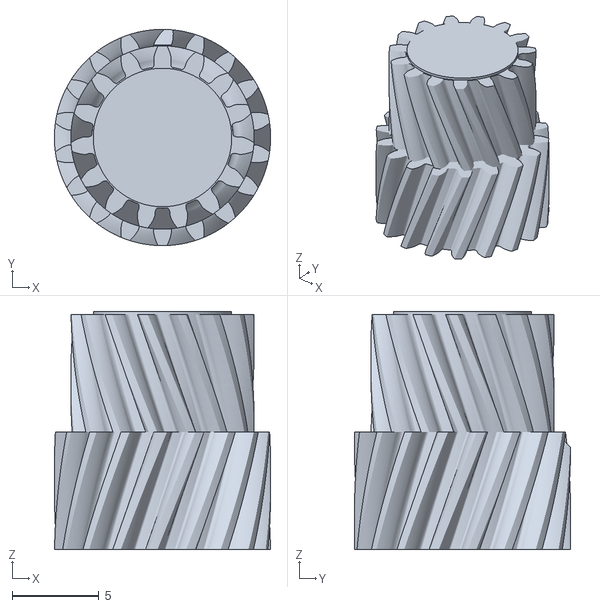
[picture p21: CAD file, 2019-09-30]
stl/PlanetClusterH40.STL
12.5 x 12.5 x 13.8

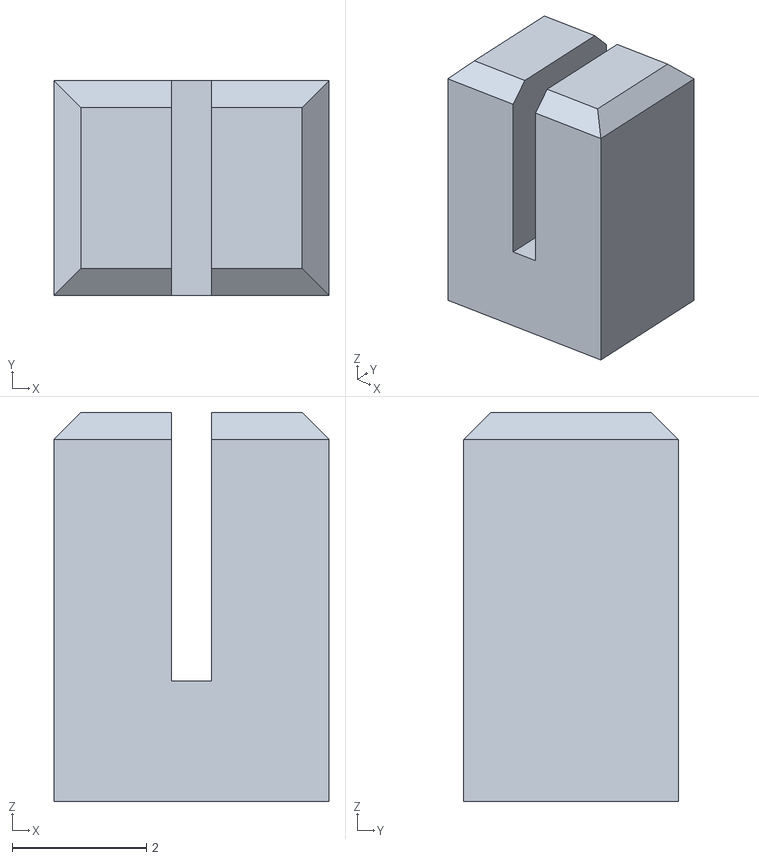
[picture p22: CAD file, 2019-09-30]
stl/hall plug.stl
4.10 x 3.20 x 5.80

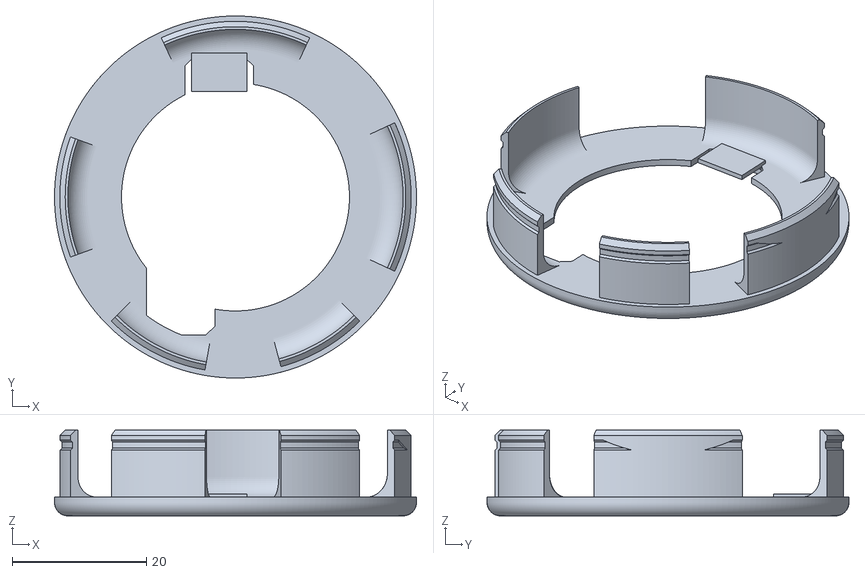
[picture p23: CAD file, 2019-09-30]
stl/shell cap 6.stl
54.0 x 54.0 x 12.8

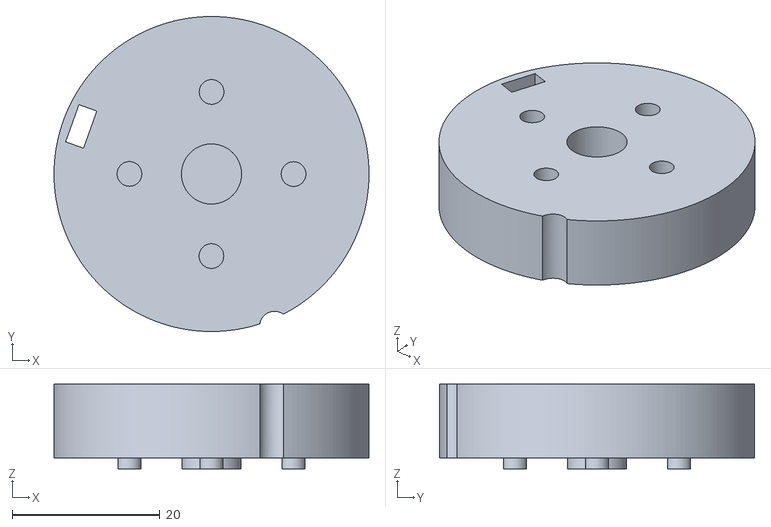
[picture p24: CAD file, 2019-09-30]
stl/support jig.stl
42.7 x 42.7 x 11.5

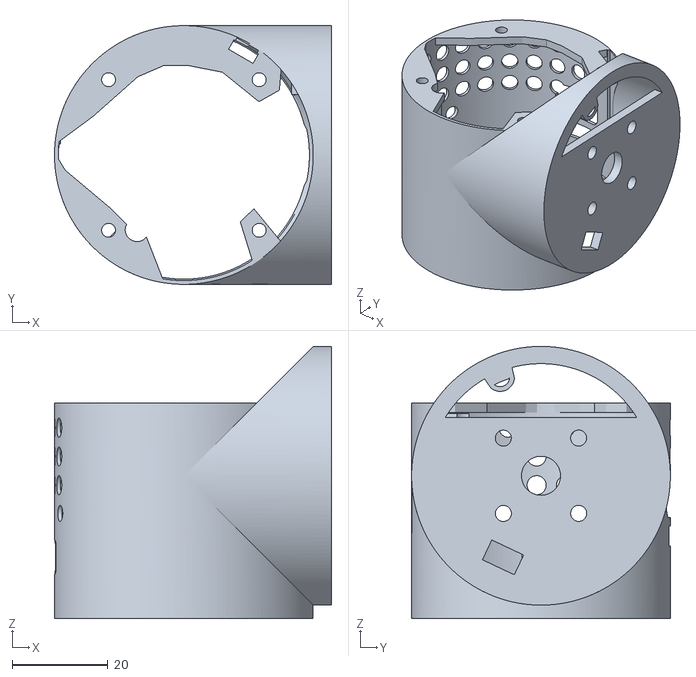
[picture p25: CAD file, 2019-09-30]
stl/cyl shell 9-20.stl
57.8 x 54.0 x 56.8

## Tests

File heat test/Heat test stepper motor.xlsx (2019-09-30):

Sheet: Sheet1
 | Room Temperature to 40 Degrees C
 | Timestamp | TempC 0% Fan | TempF |  | Timestamp | TempC 50% Fan | TempF |  | Timestamp | TempC 100% Fan | TempF |  |  | Timestamp | TempC 70% Fan | TempF
0 | 5434 | 22.6 | 72.7 | 0 | 6759 | 22.6 | 72.7 | 0 | 8530 | 22.7 | 72.9 |  | 0 | 11310 | 22.6 | 72.7
2 | 5436 | 22.7 | 72.9 | 2 | 6761 | 22.6 | 72.7 | 3 | 8533 | 22.6 | 72.7 |  | 3 | 11313 | 22.6 | 72.7
4 | 5438 | 22.7 | 72.9 | 4 | 6763 | 22.6 | 72.7 | 5 | 8535 | 22.6 | 72.7 |  | 5 | 11315 | 22.6 | 72.7
6 | 5440 | 22.8 | 73 | 7 | 6766 | 22.7 | 72.9 | 7 | 8537 | 22.6 | 72.7 |  | 7 | 11317 | 22.7 | 72.9
8 | 5442 | 22.9 | 73.2 | 9 | 6768 | 22.7 | 72.9 | 9 | 8539 | 22.7 | 72.9 |  | 9 | 11319 | 22.7 | 72.9
10 | 5444 | 23 | 73.4 | 11 | 6770 | 22.8 | 73 | 11 | 8541 | 22.7 | 72.9 |  | 11 | 11321 | 22.7 | 72.9
13 | 5447 | 23 | 73.4 | 13 | 6772 | 22.9 | 73.2 | 14 | 8544 | 22.8 | 73 |  | 14 | 11324 | 22.8 | 73
15 | 5449 | 23.1 | 73.6 | 15 | 6774 | 22.9 | 73.2 | 16 | 8546 | 22.8 | 73 |  | 16 | 11326 | 22.8 | 73
17 | 5451 | 23.2 | 73.8 | 18 | 6777 | 23 | 73.4 | 18 | 8548 | 22.9 | 73.2 |  | 18 | 11328 | 22.9 | 73.2
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

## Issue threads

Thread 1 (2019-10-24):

Small stepper motor torque rating?

Donald-Nordwick, 2019-10-24:
Do you know what the relative torque is for the smaller stepper motors from aliexpress? https://www.aliexpress.com/item/2054451318.html

I bought a few stepper motors from stepperonline that are rated at 7 Ncm and they're having issues even after using some grease.
https://www.omc-stepperonline.com/il-giro-nema-14-bipolare-0-9deg-5ncm-7-08oz-in-0-5a-8-5v-f36x12mm-4-fili.html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

chilipeppr, 2019-10-24:
Look at that moon's stepper motor I put in the bom.  The ones I got from AliExpress have very similar characteristics. The omc one you're showing is 0.9 degree instead of 7.8 degree so that is a big difference and mine are all about 150ma and yours is 500ma which makes me think yours is way stronger.

Did you break in your gears? I find that I sometimes have to print the planetary gears at 99 percent depending on printer differences.

chilipeppr, 2019-10-24:
I am not able to stop the bare shaft with my fingers on my small steppers.

Donald-Nordwick, 2019-11-05:
Thanks for the response. I was able to get it to move, I just have to work on getting those gears filed down. I was looking at step pulse loopback on eagle for the pcb and its listed as 0 ohm. Is that a typo?

chilipeppr, 2019-11-05:
The step pulse loopback is not a typo. It is a loopback. The track overlaps to connect the nets it if you cut the track out a 0 ohm to reconnect

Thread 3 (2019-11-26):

Error with rmttx_stepper_queue_v4

mcmadhatter, 2019-11-26:
I tried uploading and running the lua code, but I get and error on startup

 [0;32mI (468406) gpio: GPIO[16]| InputEn: 0| OutputEn: 1| OpenDrain: 0| Pullup: 0| Pulldown: 0| Intr:0  [0m
Slept DRV8825
loop or previous error loading module 'rmttx_stepper_queue_v4'

chilipeppr, 2019-11-26:
You have to upload all of the code in the lua folder to your ESP32 first,
make sure it's compiled to .lc files, then you won't get that error because
it will find the library.

On Tue, Nov 26, 2019 at 2:36 PM mcmadhatter <notifications@github.com>
wrote:

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

mcmadhatter, 2019-11-26:
I've uploaded the 13 lua files that are in the repo, and compiled all to .lc flies.

The only ones that are in the chilipeppr.png that are not in the repo are fan_temp_ctrl.lua tmp36_v2.lua gcode_jog_btns.lua and gcode.txt
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

chilipeppr, 2019-11-27:
Ok, just re-checked in my latest code. What a pain transferring out of ChiliPeppr into Github. I need a better way to use a Github repo in ChiliPeppr!

This is a pretty big difference using my latest code. The main entry point is main_cayenn_robot_v5.lua as you'll see in init.lua. This is now using Cayenn so you can see the actuator show up in the Cayenn widget in ChiliPeppr inside the ESP32 workspace and the robot workspace, which is working kinda/sorta now with the Axes widget in upper right corner.

Let me know how it goes.

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

mcmadhatter, 2019-11-27:
Hi , with the latest it gets a bit further before a kernel panic. I should be using the NodeMCU-touch-pulsecnt-rmttx.bin in the firmware folder shouldn't I?

NodeMCU ESP32 build unspecified powered by Lua 5.1.4 on SDK IDF
 [0;32mI (336) gpio: GPIO[16]| InputEn: 0| OutputEn: 1| OpenDrain: 0| Pullup: 0| Pulldown: 0| Intr:0  [0m
Slept DRV8825
Initted fan & temp sensor. Freq:30, Duty:8192
Apppending
Initted Gcode file save/retrieve
Initting ws2812. Using channel 7. GPIO 26. memBlocks 1
Guru Meditation Error: Core  0 panic'ed (LoadProhibited). Exception was unhandled.
Core 0 register dump:
PC      : 0x40147b01  PS      : 0x00060a30  A0      : 0x80147cd0  A1      : 0x3ffbc1b0
A2      : 0x3ffc0d3c  A3      : 0x00000000  A4      : 0x00000000  A5      : 0x3ffcd944
A6      : 0x3ffcd954  A7      : 0x00000000  A8      : 0x80147491  A9      : 0x3ffbc160
A10     : 0x3ffc7f58  A11     : 0x3ffc15c8  A12     : 0x00001800  A13     : 0x00000800
A14     : 0x00000001  A15     : 0x00000000  SAR     : 0x0000001b  EXCCAUSE: 0x0000001c
EXCVADDR: 0x00000000  LBEG    : 0x400014fd  LEND    : 0x4000150d  LCOUNT  : 0xfffffffd

ELF file SHA256: a239507fd8d32e86f79312bdb2015e39d7edf86abcf3757da8f7e68d121d0aac

Backtrace: 0x40147b01:0x3ffbc1b0 0x40147ccd:0x3ffbc1d0 0x401472f7:0x3ffbc200 0x40145470:0x3ffbc220 0x400d49c9:0x3ffbc240 0x4013d777:0x3ffbc270 0x40143b61:0x3ffbc2b0 0x4013d84e:0x3ffbc300 0x401452a5:0x3ffbc320 0x40168afe:0x3ffbc340 0x4013d777:0x3ffbc360 0x40143b61:0x3ffbc3a0 0x4013d84e:0x3ffbc3f0 0x401447cd:0x3ffbc410 0x4013d095:0x3ffbc430 0x4013d936:0x3ffbc4b0 0x401452e6:0x3ffbc4e0 0x4013f57c:0x3ffbc510 0x4013f86d:0x3ffbc530 0x4013d777:0x3ffbc560 0x4013d845:0x3ffbc5a0 0x40144811:0x3ffbc5c0 0x4013d095:0x3ffbc5e0 0x4013d936:0x3ffbc660 0x40145316:0x3ffbc690 0x4013f9f6:0x3ffbc6c0 0x400f8f51:0x3ffbc6f0 0x400d269f:0x3ffbc730

Rebooting...

chilipeppr, 2019-11-27:
Hmm. I better send you my latest firmware. It could be that.

On Wed, Nov 27, 2019 at 1:12 PM mcmadhatter <notifications@github.com>
wrote:

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

chilipeppr, 2019-11-27:
ok, just checked in my oct 4th firmware build. try that.

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

mcmadhatter, 2019-11-27:
Hi, I flashed the new firmware

```
 ~/Programming/robot-actuator-esp32-v8/firmware   master ● ⍟2  esptool.py --port /dev/cu.Repleo-CP2102-01DB132C write_flash 0x1000 bootloader.bin 0x10000 NodeMCU-touch-pulsecnt-rmttx.bin 0x8000 partitions_singleapp.bin
esptool.py v2.6
Serial port /dev/cu.Repleo-CP2102-01DB132C
Connecting.....
Detecting chip type... ESP32
Chip is ESP32D0WDQ6 (revision 1)
Features: WiFi, BT, Dual Core, 240MHz, VRef calibration in efuse, Coding Scheme None
MAC: 24:0a:c4:c6:7b:f0
Uploading stub...
Running stub...
Stub running...
Configuring flash size...
Auto-detected Flash size: 4MB
Compressed 22656 bytes to 14177...
Wrote 22656 bytes (14177 compressed) at 0x00001000 in 1.2 seconds (effective 145.1 kbit/s)...
Hash of data verified.
Compressed 998560 bytes to 639050...
Wrote 998560 bytes (639050 compressed) at 0x00010000 in 56.6 seconds (effective 141.2 kbit/s)...
Hash of data verified.
Compressed 3072 bytes to 103...
Wrote 3072 bytes (103 compressed) at 0x00008000 in 0.0 seconds (effective 1668.3 kbit/s)...
Hash of data verified.

Leaving...
Hard resetting via RTS pin...
```
interestingly it now crashes sooner than with the old firmware:

`Mounting flash filesystem...
I (418) wifi: wifi driver task: 3ffc321c, prio:23, stack:3584, core=0
 [0;32mI (418) system_api: Base MAC address is not set, read default base MAC address from BLK0 of EFUSE [0m
 [0;32mI (418) system_api: Base MAC address is not set, read default base MAC address from BLK0 of EFUSE [0m
I (438) wifi: wifi firmware version: ec61a20
I (438) wifi: config NVS flash: enabled
I (438) wifi: config nano formating: disabled
I (448) wifi: Init dynamic tx buffer num: 32
I (448) wifi: Init data frame dynamic rx buffer num: 32
I (448) wifi: Init management frame dynamic rx buffer num: 32
I (458) wifi: Init management short buffer num: 32
I (458) wifi: Init static rx buffer size: 1600
I (468) wifi: Init static rx buffer num: 10
I (468) wifi: Init dynamic rx buffer num: 32

NodeMCU ESP32 build unspecified powered by Lua 5.1.4 on SDK IDF
 [0;32mI (498) gpio: GPIO[16]| InputEn: 0| OutputEn: 1| OpenDrain: 0| Pullup: 0| Pulldown: 0| Intr:0  [0m
Slept DRV8825
ets Jun  8 2016 00:22:57

rst:0xc (SW_CPU_RESET),boot:0x13 (SPI_FAST_FLASH_BOOT)
`

mcmadhatter, 2019-11-27:
Just a thought can esptool dump the filesystem from an esp32, so it can be flashed to another esp32?

chilipeppr, 2019-11-27:
I'm not sure if esptool can do that, but there is an Upload All button in
ChiliPeppr to send all of that code to the ESP32 without much effort other
than just waiting around for it all to upload. It makes a nice ding sound
when it's done uploading all of the files.

On Wed, Nov 27, 2019 at 3:26 PM mcmadhatter <notifications@github.com>
wrote:

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

chilipeppr, 2019-11-27:
[image: image.png]

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

chilipeppr, 2019-11-27:
On your error, it does look like you're seeing a  SW_CPU_RESET which is
weird to me. That's as if it ran code that did a node.restart()

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
>>> Just a thought can esptool dump the filesystem from an esp32, so it can
>>> be flashed to another esp32?
>>>
>>> —
>>> You are receiving this because you commented.
>>> Reply to this email directly, view it on GitHub
>>> <https://github.com/chilipeppr/robot-actuator-esp32-v8/issues/3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>,
>>> or unsubscribe
>>> <https://github.com/notifications/unsubscribe-auth/AB4J23N4DOC7RIURSQPOMA3QV3627ANCNFSM4JR6XA7Q>
>>> .
>>>
>>

mcmadhatter, 2019-11-27:
esptool.py --port <your port>  read_flash 0 0x400000 flash_contents.bin   will dump everything including the filesystem.

Would you be ok to try doing that on your working chip, and sending me the flash_contents.bin to try on mine?

chilipeppr, 2019-11-28:
I'm not near any of my ESP32 devices, sorry.

On Wed, Nov 27, 2019 at 3:55 PM mcmadhatter <notifications@github.com>
wrote:

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

mcmadhatter, 2019-11-28:
OK, no worries.

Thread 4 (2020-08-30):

Unknown Value for R1 resistor

karlmueller, 2020-08-30:
There are resistor values in the BOM for all resistors except for R1. The resistor in question is located next to a STEP callout and is circled in the enclosed CAD rendering. Please update the BOM to include this resistor value.

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

chilipeppr, 2020-08-30:
There is no resistor needed there. That is a 0 ohm resistor, meaning it's a wire, and the wire is actually connected in the Eagle BRD file so you don't need to do anything there.

The point of that 0 ohm resistor is that the ESP32 is supposed to be able to do internal loopbacks inside the chip itself so that you can send PWM out one GPIO and do a pulsecnt on another GPIO. However, I was never able to get that to work via the code so I just did it via the external wiring to loop back the signal. If I figured it out eventually in the software, I wanted to have a way to cut the wire and possibly re-solder if I needed to.

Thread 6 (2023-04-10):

Torque capabilities?

TTD1024, 2023-04-10:
Are there figures for torque tests of this actuator anywhere? I've been watching through the videos, great work, but hadn't spotted figures anywhere giving the torque capability and noting whether, if suficiently overloaded, the motor would stall first or the gears would fracture?
Thanks

chilipeppr, 2023-04-10:
Never got around to any torque tests but I'd guess 1 to 2Nm. This arm can't lift much beyond it's own weight. The motors just miss steps. The gears are fine actually.

TTD1024, 2023-04-16:
Thanks

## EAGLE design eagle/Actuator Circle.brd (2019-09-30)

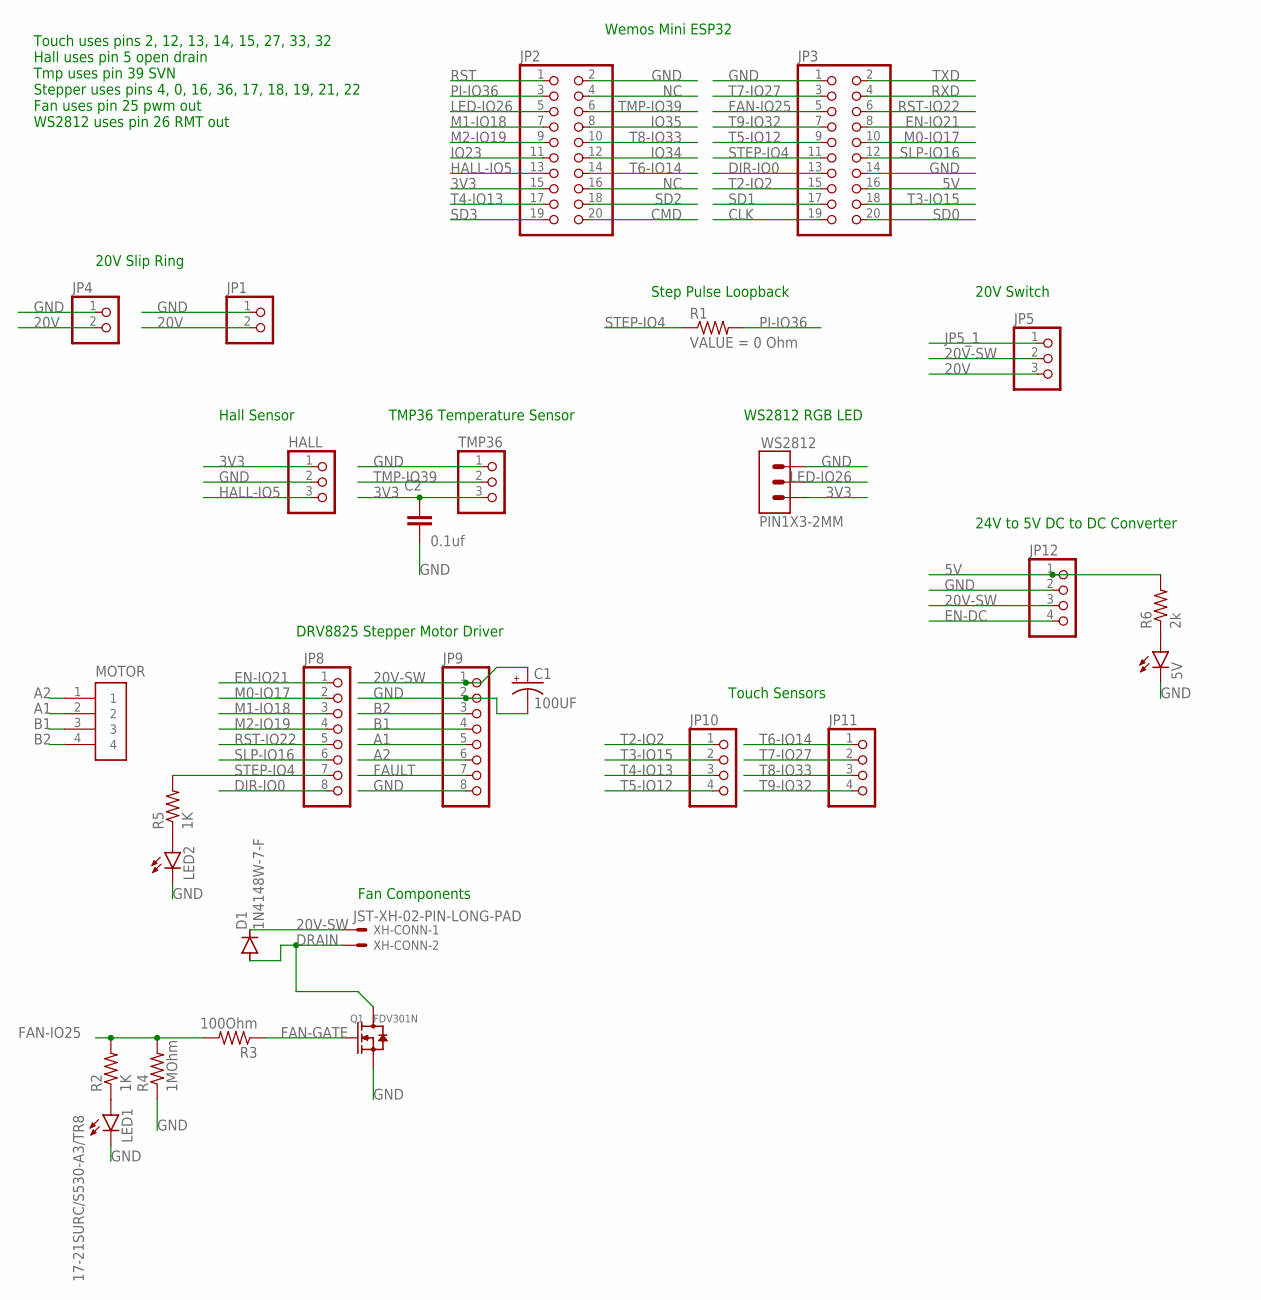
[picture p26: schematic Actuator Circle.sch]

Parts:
5V: 17-21SURC/S530-A3/TR8; CHIPLED_0805
C1: 100UF; E2,5-6
C2: 0.1uf; CAP_0603
D1: 1N4148W-7-F; SOD123
HALL: PINHD-1X3; 1X03
JP1, JP4: PINHD-1X2; 1X02
JP2, JP3: PINHD-2X10; 2X10
JP5: PINHD-1X3/90; 1X03/90
JP8, JP9: PINHD-1X8; 1X08
JP10, JP11, JP12: PINHD-1X4; 1X04
LED1, LED2: 17-21SURC/S530-A3/TR8; CHIPLED_0805
MOTOR: B4B-PH-K-S(LF)(SN); JST_B4B-PH-K-S(LF)(SN)
Q1: FDV301N; SOT23
R1: 0 Ohm; RES_0402
R2, R5: 1K; RES_0402
R3: 100Ohm; RES_0402
R4: 1MOhm; RES_0402
R6: 2k; RES_0402
TMP36: PINHD-1X3; 1X03
WS2812: PIN1X3-2MM
XH-CONN: JST-XH-02-PIN-LONG-PAD; JST-XH-02-PACKAGE-LONG-PAD

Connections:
3V3: C2.1, HALL.1, JP2.15, TMP36.3, WS2812.3
5V: JP3.16, JP12.1, R6.2
20V: JP1.2, JP4.2, JP5.3
20V-SW: C1.+, D1.1 (C), JP5.2, JP9.1, JP12.3, XH-CONN.1
A1: JP9.5, MOTOR.2
A2: JP9.6, MOTOR.1
B1: JP9.4, MOTOR.3
B2: JP9.3, MOTOR.4
CLK: JP3.19
CMD: JP2.20
DIR-IO0: JP3.13, JP8.8
DRAIN: D1.2 (A), Q1.3 (D), XH-CONN.2
EN-DC: JP12.4
EN-IO21: JP3.8, JP8.1
FAN-GATE: Q1.1 (G), R3.1
FAN-IO25: JP3.5, R2.2, R3.2, R4.2
FAULT: JP9.7
GND: 5V.C, C1.-, C2.2, HALL.2, JP1.1, JP2.2, JP3.1, JP3.14, JP4.1, JP9.2, JP9.8, JP12.2, LED1.C, LED2.C, Q1.2 (S), R4.1, TMP36.1, WS2812.1
HALL-IO5: HALL.3, JP2.13
IO23: JP2.11
IO34: JP2.12
IO35: JP2.8
JP5_1: JP5.1
LED-IO26: JP2.5, WS2812.2
M0-IO17: JP3.10, JP8.2
M1-IO18: JP2.7, JP8.3
M2-IO19: JP2.9, JP8.4
unnamed: LED1.A, R2.1
unnamed: LED2.A, R5.1
unnamed: 5V.A, R6.1
NC: JP2.4, JP2.16
PI-IO36: JP2.3, R1.2
RST: JP2.1
RST-IO22: JP3.6, JP8.5
RXD: JP3.4
SD0: JP3.20
SD1: JP3.17
SD2: JP2.18
SD3: JP2.19
SLP-IO16: JP3.12, JP8.6
STEP-IO4: JP3.11, JP8.7, R1.1, R5.2
T2-IO2: JP3.15, JP10.1
T3-IO15: JP3.18, JP10.2
T4-IO13: JP2.17, JP10.3
T5-IO12: JP3.9, JP10.4
T6-IO14: JP2.14, JP11.1
T7-IO27: JP3.3, JP11.2
T8-IO33: JP2.10, JP11.3
T9-IO32: JP3.7, JP11.4
TMP-IO39: JP2.6, TMP36.2
TXD: JP3.2

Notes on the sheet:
Touch Sensors
DRV8825 Stepper Motor Driver
Wemos Mini ESP32
Fan Components
24V to 5V DC to DC Converter
20V Slip Ring
Hall Sensor
TMP36 Temperature Sensor
WS2812 RGB LED
Touch uses pins 2, 12, 13, 14, 15, 27, 33, 32 Hall uses pin 5 open drain Tmp uses pin 39 SVN Stepper uses pins 4, 0, 16, 36, 17, 18, 19, 21, 22 Fan uses pin 25 pwm out WS2812 uses pin 26 RMT out
Step Pulse Loopback
20V Switch

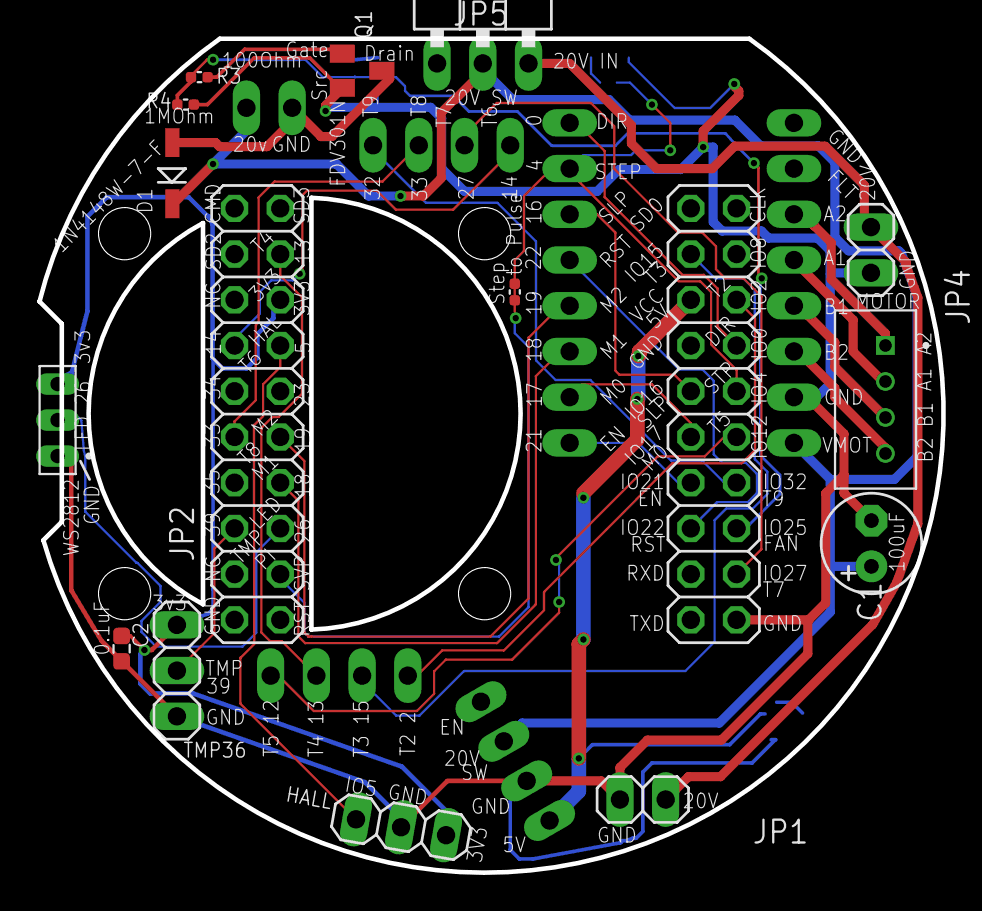
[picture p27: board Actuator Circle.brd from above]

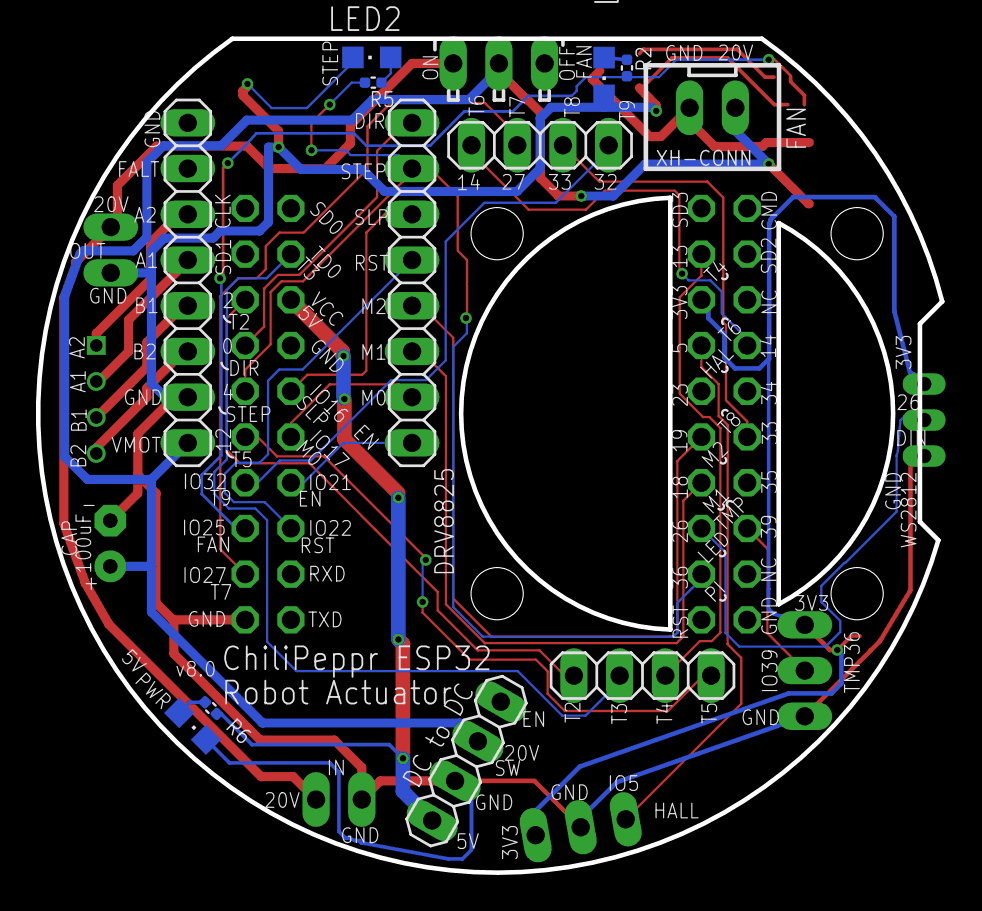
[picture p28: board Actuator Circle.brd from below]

Board: 2 copper layers, 50.2 x 46.3 mm, 28 parts (12 on the bottom side), 36 nets.

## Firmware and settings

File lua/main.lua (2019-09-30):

-- Actuator Jog Gcode Buttons

-- local m = {}
m = {}

m.led = require("rmttx_ws2812_v2")
m.jog = require("jog_v3")
m.file = require("gcode_file")
m.touch = require("touch_8pads_jog_ws2812")
m.motor = require("drv8825_driver_v1")
m.endstop = require("hall_endstop")
m.homing = require("homing_v1")
m.gcode = require("rmttx_stepper_queue_v4")
m.pcnt = require("pulsecnt_machine")

dofile("fan_temp_ctrl.lc")

-- in case you need to invert direction pin due to wiring differences
-- on stepper motor
m.isInvert = true 

-- if you want the jog frequency to increment in greater/lower amounts
-- during use of the touch dial, default is 10, 
-- try 20, 30, or 40 for faster
-- for finer control use a lower number like 5
m.jogFreqIncrement = 5

function m.init()
  
  -- init saving and reading of gcode from Flash memory
  m.file.init()
  
  -- init our LED WS2812 library
  m.led.init()
  
  -- init our motor
  m.motor.init({
    isInvert = m.isInvert, -- invert the dirFwd/dirRev (in case your wiring is reversed)
    isDebug = false,
  })
  
  -- init pulse counter library
  m.pcnt.init({
    isInvert = m.isInvert, -- invert the dirFwd/dirRev (in case your wiring is reversed)
    pinDir = m.motor.pinDir,
    pinPulseInput = m.motor.pinPulseInput,
    stepLimitMax = 32767,
    stepLimitMin = -32767
  })

  -- init our jogging
  m.jog.init({
    onJogPause = m.onJogPause,
    motor = m.motor, -- in case they passed us a drv8825 lib, nil is safe
  })

  -- init jogging. sets up touch pads, freq generator for stepper,
  -- and drv8825 driver
  m.touch.init({
    jogFreqIncrement = m.jogFreqIncrement, -- ask for touch dial speed
    cbOnCenterBtnTouch=m.onCenterBtnTouch,
    jog = m.jog,
    led = m.led,
    isDebug=false
  })
  m.touch.config() -- sets thresholds on pads. don't touch pads during config.
  
  -- init the endstop library
  m.endstop.init({
    onHit = m.onEndstopHit,
    onLeave = m.onEndstopLeave,
    isDebug = true
  })

  -- init the homing library
  m.homing.init({
    motor = m.motor,
    jog = m.jog,
    cbOnHomingStep = m.onHomingStep,
    isDebug = false,
  })

  -- init the gcode library which lets us send via RMT hardware the steps
  -- this does bind the RMT hardware to the step GPIO
  -- so need to toggle back jog GPIO
  m.gcode.init({
    cbOnMoveDone = m.onGcodeMoveDone,
    pcnt = m.pcnt,
    motor = m.motor,
  })

  -- ok, now that we have the jogging library and gcode library initted
  -- we have to map the step pin to allow inputs from ledc and rmttx
  -- the rmttx is in control right now because it was last instantiated
  

  -- m.gcode.runGcodeAbs({step=100})
  
  -- even though no gcode playing, stop it so that it starts jog listening
  m.gcodeStop()

  -- Home the actuator
  m.homing.home()
  
  
end

function m.onHomingStep(homeStep)
  m.printCoords()
  print("Home step:", homeStep)
  
  if homeStep == "done" then
    m.led.blink(0,0,255, 30,0,30)
  else
    m.led.blink(0,0,40, 0,0,10)
  end
end

function m.onEndstopHit()
  print("Got endstop hit")
  if m.homing.getState() ~= "" then
    -- we were homing, so call the homing method back so it can do next step
    local result = m.homing.home()

  end
    
end

function m.onEndstopLeave()
  print("Got endstop leave")
  if m.homing.getState() ~= "" then
    -- we were homing, so call the homing method back so it can do next step
    local result = m.homing.home()
    
    if result == "done" then
      -- Set machine coords to zero, i.e. pulse counter
      m.pcnt.setMachineCoordsToZero()
      -- Set accel stepper to zero as well
      m.gcode.setMachineCoords(0)
      m.printCoords()
    end
    
  end
end

-- Get callback on center button touched
-- event:0 is touch, event:1 is untouch
-- Return true to preventDefault
function m.onCenterBtnTouch(event, usec)
  print("Got onCenterBtnTouch. event:", event, "usec:", usec)
  
  if event == 0 then
    print("Got center btn touch")
  elseif event == 1 then
    
    local secs = usec / 1000000
    print("Got center btn untouch. secs:", secs, "usec:", usec)
    
    -- see if they long press for more than 10 or 4 seconds
    -- 10 secs wipe gcode
    -- 4 secs record position
    if secs > 12 then
      -- do homing
      m.homing.home()
    elseif secs > 6 then
      -- go red to indicate wipe
      m.led.blink(255,0,0, 30,0,30)
      m.file.wipe()
      print("Wiped Gcode")
    elseif secs > 3  then
      -- blink green to indicate record
      m.led.blink(0,255,0, 30,0,30)
      
      local gcode = {
        step=m.pcnt.getMachineCoords(),
        -- fr=100,
        -- acc=100,
      }
      m.file.write(gcode)
      print("Recording Gcode:", sjson.encode(gcode))
    elseif secs > 1 then
      
      if m._isGcodePlaying then
        print("Asking to stop playing Gcode")
        -- m.gcodeStop()
        m.gcodeAskForStop()
      else
        print("Start playing Gcode")
        m.gcodePlay()
      end
    else
      print("Short tap. Does nothing for now.")
    end
    
  end
end

function m.printCoords()
  print("Coords. Pcnt:", m.pcnt.getMachineCoords(), "RmtStep:", m.gcode.getMachineCoords())
end

function m.onJogPause()
  print("Got onJogPause")
  -- we have to update the gcode library that we are at a different position
  m.gcode.setMachineCoords(m.pcnt.getMachineCoords())
  m.printCoords()
end

m._isNonFileMove = false
m._nonFileMove = nil
function m.gcodeRunOneMove(move)
  m._isNonFileMove = true
  m._nonFileMove = move
  m.gcodePlay()
end

function m.gcodeGetNext()
  if m._isNonFileMove then
    -- if entering here with nil move, then it's 2nd re-entrant, which means we're done
    -- so set _isNonFileMove to false
    if m._nonFileMove == nil then m._isNonFileMove = false end
    -- set to nil for so next time re-entering this method we can recognize the step
    local move = m._nonFileMove
    m._nonFileMove = nil 
    return move
  else 
    return m.file.getNext()
  end
end

function m.gcodePlay()
  m._isGcodePlaying = true
  m._isAskedForStop = false
  
  -- show green on led as playing gcode
  m.led.blink(0,255,0, 0,100,0)
  
  -- make sure jogging is off and rebind gcode lib
  m.jog.stop()
  m.gcode.rmtstep.bind()
  
  -- read a line, insert to queue, play the queue
  -- get callback of onGcodeMoveDone() when line done playing
  -- so we can get next
  m.file.close()
  m.file.openRead()
  local qItem = m.gcodeGetNext() --m.file.getNext()
  if qItem ~= nil then
    -- we have a line
    m.gcode.runGcodeAbs(qItem)
  else
    print("There was no Gcode to play")
    m.gcodeStop()
  end
end

m._isAskedForStop = false
function m.gcodeAskForStop()
  m._isAskedForStop = true
end

function m.gcodeStop()
  m._isGcodePlaying = false
  m.motor.disable()
  
  -- go purple bright, then purple dim
  m.led.blink(255,0,255, 30,0,30)
  
  -- unbind gcode lib RMT hardware from pinStep
  -- rebind jogging LEDC pwm generator to pinStep
  m.gcode.rmtstep.unbind()
  m.jog.start()

end

function m.onGcodeMoveDone()
  print("Got onGcodeMoveDone")
  m.led.blink(0,30,0, 0,100,0)
  m.printCoords()
  
  if m._isAskedForStop then
    -- don't do next line
    print("User asked to stop gcode, so stopping.")
    m.gcodeStop()
    return
  end
  
  -- do next line
  local qItem = m.gcodeGetNext()
  if qItem ~= nil then
    -- we have a line
    m.gcode.runGcodeAbs(qItem)
  else
    print("Done playing gcode")
    m.gcodeStop()
  end
end

m.init()

return m

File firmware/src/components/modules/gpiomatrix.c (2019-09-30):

/* 
GPIO Matrix allows you to redirect all signals inside of the ESP32 to any/all GPIO.
Authored by: ChiliPeppr (John Lauer) 2019

ESP32 has roughly 40 GPIOs, but it also has about 100 peripheral signals from 
sub-systems such as RMT, LEDC, MCPWM, I2S, CAN, etc. Together this 
is over 150 signals. You can re-route and connect any of these signals to each other via 
the GPIO matrix including one-to-many and many-to-one.

This code is in the Public Domain (or CC0 licensed, at your option.)
Make modifications at will and freely.

Unless required by applicable law or agreed to in writing, this
software is distributed on an "AS IS" BASIS, WITHOUT WARRANTIES OR
CONDITIONS OF ANY KIND, either express or implied.
*/

#include "module.h"
#include "lauxlib.h"
#include "lmem.h"

#include "driver/gpio.h"
#include "soc/gpio_sig_map.h"

#include <assert.h>

// Lua: gpiomatrix.periphOutToGpioIn(periph, gpio)
// Example:
//   -- Map LEDC peripheral output to GPIO that Pulse Counter listens on 
//   gpiomatrix.periphOutToGpioIn(
//     gpiomatrix.LEDC_HS_SIG_OUT0_IDX, -- Peripheral
//     gm.pinPulseCnt  -- GPIO
//   )
static int gpiomatrix_periphOutToGpioIn( lua_State *L ) {

  int periph = luaL_checkint (L, 1);
  int gpio = luaL_checkint (L, 2);

  // In this example below, pin_number is the GPIO pin number. io_signal_in and io_signal_out are values 
  // identifying the peripheral and signal you want to route: signal numbers can be found in 
  // esp-idf/components/soc/esp32/include/soc/gpio_sig_map.h . Use *_IN_IDX as possible values 
  // for io_signal_in, *_OUT_IDX for io_signal_out.

  // Connect the pin to the GPIO matrix.
  // PIN_FUNC_SELECT(GPIO_PIN_MUX_REG[pin_number], PIN_FUNC_GPIO);

  // Set the direction. GPIO_MODE_INPUT always makes it an input, GPIO_MODE_OUTPUT always makes it 
  // an output, GPIO_MODE_INPUT_OUTPUT lets the peripheral decide what direction it has. You usually 
  // want the last one.
  // gpio_set_direction(gpio, GPIO_MODE_INPUT_OUTPUT);

  // Connect the output functionality of a peripheral to the pin you want. This allows a peripheral 
  // to set the direction of the pin (in case it's configured as GPIO_INPUT_OUTPUT) and set the 
  // output value. *_OUT_IDX
  gpio_matrix_out(gpio, periph, false, false);

  // Connect the input functionality of a peripheral to the pin. This allows the peripheral to 
  // read the signal indicated from this pin. *_IN_IDX
  // gpio_matrix_in(pin_number, *_IN_IDX, false);
  return 0;
}

// Lua: gpiomatrix.gpioOutToPeriphIn(gpio, periph)
// Example:
//   -- Map LEDC GPIO output pin to Pulse Counter peripheral 
//   gpiomatrix.gpioOutToPeriphIn(
//     gm.pinLedc, -- GPIO
//     gpiomatrix.PCNT_SIG_CH0_IN0_IDX -- Peripheral
//   )
static int gpiomatrix_gpioOutToPeriphIn( lua_State *L ) {

  int gpio = luaL_checkint (L, 1);
  int periph = luaL_checkint (L, 2);

  // Connect the input functionality of a peripheral to the pin. This allows the peripheral to 
  // read the signal indicated from this pin.
  gpio_matrix_in(gpio, periph, false);

  return 0;
}

// static int gpiomatrix_iomuxGpioOutToPeriphIn( lua_State *L ) {

//   int gpio = luaL_checkint (L, 1);
//   int periph = luaL_checkint (L, 2);

//   // Connect the input functionality of a peripheral to the pin. This allows the peripheral to 
//   // read the signal indicated from this pin.
//   gpio_matrix_in(gpio, periph, false);

//   return 0;
// }

// Lua: gpiomatrix.setDir(gpio, dir)
static int gpiomatrix_setDir( lua_State *L ) {

  int gpio = luaL_checkint (L, 1);
  int dir = luaL_checkint (L, 2);

  // Connect the pin to the GPIO matrix.
  // PIN_FUNC_SELECT(GPIO_PIN_MUX_REG[pin_number], PIN_FUNC_GPIO);
  // Set the direction. GPIO_MODE_INPUT always makes it an input, GPIO_MODE_OUTPUT always makes it 
  // an output, GPIO_MODE_INPUT_OUTPUT lets the peripheral decide what direction it has. You usually 
  // want the last one.
  gpio_set_direction(gpio, dir);

  return 0;
}

// Lua: gpio.write(gpio, 0 || 1)
/*
static int lgpio_write (lua_State *L)
{
  int gpio = luaL_checkint (L, 1);
  int level = luaL_checkint (L, 2);
  check_err (L, gpio_set_level (gpio, level));
  return 0;
}
*/

static int gpiomatrix_init (lua_State *L)
{
  return 0;
}
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

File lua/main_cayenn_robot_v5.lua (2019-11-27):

-- Main entry point for ChiliPeppr Robot Actuator
-- Stepper jogging/homing, Fan control, Temperature
-- We also report back status on a 1 second interval (temperature, fan, steps, current)

-- init cayenn
cayenn = require("cayenn_esp32_v4")

-- **** User Defined Variables **********
cayenn.ssid = "NETGEAR-main"
cayenn.password = "****"

-- opts = {
--   Name = "Wrist3",
--   Icon = "https://raw.githubusercontent.com/chilipeppr/widget-robot-axes/master/Wrist3.jpg",
--   Desc = "Actuator controller",
--   IsInvert = true,
-- }

opts = {
  Name = "Wrist2",
  Icon = "https://raw.githubusercontent.com/chilipeppr/widget-robot-axes/master/Wrist2.jpg",
  Desc = "Actuator controller",
  IsInvert = false,
}

ignoreIp = "10.0.0.56"
-- **** End User Defined Variables **********

-- init libraries
cayenn = require("cayenn_esp32_v4")
json = sjson -- map sjson to json
queue = require("queue") -- Command queue
ctrl = require("gcode_jog_btns_v2") -- gets you led, motor, jog, endstop, etc.
dofile("commands_v1.lc") -- include the command list

-- Init the control library which contains all hardware control
ctrl.init({
  isInvert = opts.IsInvert
})

-- Store SPJS server ip's (can be more than one)
servers = {}

-- we can be set as master from ChiliPeppr
-- if we are, it's our job to send the signal wire high/lows
-- we should also get all the receipts back from each slave device 
-- for each command so we know we can send the signal for the next cmd 
isMaster = false

-- This is called when an incoming cmd comes in
-- from the network, i.e. from SPJS. These are TCP commands so
-- they are guaranteed to come in (vs UDP which could drop and has
-- its own callback function further down.)
function onCmd(payload)
  
  if (type(payload) == "table") then
    
    if payload.Cmd ~= nil then
      print("Got incoming Cayenn cmd: " .. payload.Cmd .. ", JSON: " .. json.encode(payload))
      -- see if we have a function to handle this. _G has all global functions in it
      if _G[payload.Cmd] then
        _G[payload.Cmd](payload)
        -- print("Handled by global func")
        return
      end
    else 
      print("Got incoming Cayenn with no cmd. JSON: " .. json.encode(payload))
    end 
    
    -- These are your custom commands you are implementing
    -- for this Cayenn device
    if payload.Cmd == "SetAsMaster" then
      -- If we are master, we have to get a "Play" command,
      -- a "Pause" command, and a "Stop" command.
    
    elseif payload.Cmd == "Restart" then
      cayenn.send({["TransId"] = payload.TransId, ["Resp"] = payload.Cmd})
      node.restart()
    elseif payload.Cmd == "TestStart" then
    
      -- Start loop on stepper 
      ctrl.jog.testStart()
      -- cayenn.send({["TransId"] = payload.TransId, ["Resp"] = payload.Cmd, ["Hz"] = payload.Hz, ["Duty"] = actualDuty})
      cayenn.send({["TransId"] = payload.TransId, ["Resp"] = payload.Cmd})
      print("Started loop test on stepper")
      
    elseif payload.Cmd == "TestStop" then
    
      ctrl.jog.testStop()
      cayenn.send({["TransId"] = payload.TransId, ["Resp"] = payload.Cmd})
      print("Stopped loop test on stepper")

    -- Below are more standard commands you should always support
    elseif payload.Cmd == "ResetCtr" then
      -- cnc.resetIdCounter()
      cayenn.send({["TransId"] = payload.TransId, ["Resp"] = payload.Cmd, ["Ctr"] = cnc.getIdCounter()})
    elseif payload.Cmd == "GetCtr" then
      cayenn.send({["TransId"] = payload.TransId, ["Resp"] = payload.Cmd, ["Ctr"] = cnc.getIdCounter()})
    elseif payload.Cmd == "GetQ" then
      -- this method will send slowly as not to overwhelm
      -- queue.send(function(t) cayenn.send(t); end, payload.TransId)
    elseif payload.Cmd == "WipeQ" then
      queue.wipe()
      cayenn.send({["TransId"] = payload.TransId, ["Resp"] = payload.Cmd})
    elseif payload.Cmd == "CmdQ" then
      -- queuing cmd. we must have ID.
      if payload.Id == nil then
        -- print("Error queuing command. It must have an ID")
        return
      end
      if payload.RunCmd == nil then
        -- print("Error queuing command. It must have a RunCmd like RunCmd:{Cmd:AugerOn,Speed:10}.")
        return
      end
      -- wipe the peerIp cuz don't need it
      payload.peerIp = nil
      -- print("Queing command")
      --queue[payload.Id] = payload.RunCmd
      payload.RunCmd.Id = payload.Id
      queue.add(payload.RunCmd)
      -- print("New queue: " .. cjson.encode(queue))
      cayenn.send({["TransId"] = payload.TransId, ["Resp"] = payload.Cmd, ["Id"] = payload.Id})
    elseif payload.Cmd == "Mem" then
      cayenn.send({["TransId"] = payload.TransId, ["Resp"] = payload.Cmd, ["MemRemain"] = node.heap()})
    elseif payload["Announce"] ~= nil then
      -- do nothing. 
      if payload.Announce == "i-am-your-server" then
        -- store this ip
        -- so we know what our SPJS server is
        
        -- we should get a ServerIp, but should also get peerIp
        -- see if they are the same. latest nodemcu firmware seems
        -- to give us a peerIp now.
        local ip = payload.ServerIp
        if ip == nil then
          ip = payload.peerIp
        end
        if ip == nil then
          print("Err: Did not get ip from server.")
        else
          -- see if in ignore list
          if (ip == ignoreIp) then
            print("Got server to ignore: "..ip)
          else
            
            -- we got a server we want, see if we already
            -- got this server and initted our TCP connection back 
            if servers[ip] then 
              print("We are already connected back to this server.")
            else 
              servers[ip] = true
              print("Got a server:" .. json.encode(servers))
              -- connect tcp_client back to the server 
              cayenn.initTcpSend(ip)
              
              -- start sending status
              -- statusStart()
              ctrl.led.pulse(0,0,80)
            end
          end
        end
      end
    else
      cayenn.send({["TransId"] = payload.TransId, ["Resp"] = payload.Cmd, ["Err"] = "Unsupported cmd"})
      -- print("Got cmd we do not understand. Huh?")
    end
  else
    -- If we are sent Cayenn commands that aren't JSON, they
    -- will get here. However, JSON should always be used.
    -- print("is string")
    -- print("Got incoming Cayenn cmd. str: ", payload)
  end
  
end
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

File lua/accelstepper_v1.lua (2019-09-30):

-- Stepper Acceleration/Deceleration for ESP32
-- This library ported from https://www.airspayce.com/mikem/arduino/AccelStepper/

local m = {}
-- m = {}

m.isDebug = false 

-- Direction of motor
m.DIRECTION_CCW = 0 -- Counter-Clockwise
m.DIRECTION_CW  = 1 -- Clockwise

-- MotorInterfaceType
-- Brief Symbolic names for number of pins.
-- Use this in the pins argument the AccelStepper constructor to 
-- provide a symbolic name for the number of pins
-- to use.
m.CALC      = -1 -- Do all normal functions but skip delay test
m.FUNCTION  = 0 -- Use the functional interface, implementing your own driver functions (internal use only)
m.DRIVER    = 1 -- Stepper Driver, 2 driver pins required

-- The target position in steps. The AccelStepper library will move the
-- motor from the _currentPos to the _targetPos, taking into account the
-- max speed, acceleration and deceleration
m._targetPos = 0 -- Steps
-- -- The current interval between steps in microseconds.
-- -- 0 means the motor is currently stopped with m._speed == 0
m._stepInterval = 0 

-- Current direction motor is spinning in
-- Protected because some peoples subclasses need it to be so
m._direction = true -- true == CW

-- Number of pins on the stepper motor. 0 is step/dir. Permits 2 or 4. 2 pins is a
-- bipolar, and 4 pins is a unipolar.
m._interface = 0         -- 0, 1, 2, 4, 8, See MotorInterfaceType

-- Arduino pin number assignments for the 2 or 4 pins required to interface to the
-- stepper motor or driver
m._pin = {1,2,3,4}

-- Whether the _pins is inverted or not
m._pinInverted = {1,2,3,4}

-- The current absolution position in steps.
m._currentPos = 0    -- Steps

-- The target position in steps. The AccelStepper library will move the
-- motor from the _currentPos to the _targetPos, taking into account the
-- max speed, acceleration and deceleration
m._targetPos = 0     -- Steps

-- The current motos speed in steps per second
-- Positive is clockwise
m._speed = 0.0        -- Steps per second

-- The maximum permitted speed in steps per second. Must be > 0.
m._maxSpeed = 0.0

-- The acceleration to use to accelerate or decelerate the motor in steps
-- per second per second. Must be > 0
m._acceleration = 1.0
m._sqrt_twoa = 0.0 -- Precomputed sqrt(2*m._acceleration)

-- The current interval between steps in microseconds.
-- 0 means the motor is currently stopped with m._speed == 0
m._stepInterval = 0

-- The last step time in microseconds
m._lastStepTime = 0

-- The minimum allowed pulse width in microseconds
m._minPulseWidth = 0

-- Is the direction pin inverted?
--/bool           _dirInverted -- Moved to m._pinInverted[1]

-- Is the step pin inverted?
--/bool           _stepInverted -- Moved to m._pinInverted[0]

-- Is the enable pin inverted?
m._enableInverted = false

-- Enable pin for stepper driver, or 0xFF if unused.
m._enablePin = nil

-- The pointer to a forward-step procedure
m._cbForward = nil --void (*_forward)()

-- The pointer to a backward-step procedure
m._cbBackward = nil--void (*_backward)()

-- The step counter for speed calculations
m._n = 0

-- Initial step size in microseconds
m._c0 = 0.0

-- Last step size in microseconds
m._cn = 0.0

-- Min step size in microseconds based on maxSpeed
m._cmin = 0.0 -- at max speed

--- Init.
-- @param interface number
-- @param pin1 number 
-- @param pin1 number 
-- @param pin1 number 
-- @param pin1 number 
-- @param enable boolean 
function m.init(interface, pin1, pin2, pin3, pin4, enable)

  m._interface = interface
  m._currentPos = 0
  m._targetPos = 0
  m._speed = 0.0
  m._maxSpeed = 1.0
  m._acceleration = 0.0
  m._sqrt_twoa = 1.0
  m._stepInterval = 0
  m._minPulseWidth = 1
  m._enablePin = 0xff
  m._lastStepTime = 0
  m._pin[1] = pin1
  m._pin[2] = pin2
  m._pin[3] = pin3
  m._pin[4] = pin4
  m._enableInverted = false
  
  -- NEW
  m._n = 0
  m._c0 = 0.0
  m._cn = 0.0
  m._cmin = 1.0
  m._direction = m.DIRECTION_CCW

  -- Some reasonable default
  m.setAcceleration(1)
  
  if m.isDebug then print("Initted") end
end

-- This method is for m.CALC or m.FUNCTION with callbacks 
-- If you pass m.CALC then no delay occurs and you can use this 
-- to calculate the data for the run.
-- @param interface MotorInterfaceType
function m.initWithCallbacks(interface, cbForward, cbBackward)

  m._interface = interface
  m._currentPos = 0
  m._targetPos = 0
  m._speed = 0.0
  m._maxSpeed = 1.0
  m._acceleration = 0.0
  m._sqrt_twoa = 1.0
  m._stepInterval = 0
  m._minPulseWidth = 1
  m._enablePin = 0xff
  m._lastStepTime = 0
  m._pin[0] = 0
  m._pin[1] = 0
  m._pin[2] = 0
  m._pin[3] = 0
  m._cbForward = cbForward
  m._cbBackward = cbBackward

  -- NEW
  m._n = 0
  m._c0 = 0.0
  m._cn = 0.0
  m._cmin = 1.0
  m._direction = m.DIRECTION_CCW

  local i
  for i = 1,4 do
    m._pinInverted[i] = 0
  end
  
  -- Some reasonable default
  m.setAcceleration(1)
end

--- Absolute position move.
-- @param absolute
-- @return nil 
function m.moveTo(absolute)
  if (m._targetPos ~= absolute) then
	  m._targetPos = absolute
	  m.computeNewSpeed()
  end
end 

--- Relative position move.
-- @param relative
-- @return nil 
function m.move(relative)
  m.moveTo(m._currentPos + relative)
end

-- Implements steps according to the current step interval
-- You must call this at least once per step
-- returns true if a step occurred
function m.runSpeed()
    -- -- Dont do anything unless we actually have a step interval
  if (m._stepInterval == 0) then return false end 

  if m._interface == m.CALC then
    -- we are in calculate only mode, so skip time check 
    
    if (m._direction == m.DIRECTION_CW) then
	    -- Clockwise
	    m._currentPos = m._currentPos + 1
  	else
	    -- Anticlockwise  
	    m._currentPos = m._currentPos - 1
  	end
  	m.step(m._currentPos)
  	return true 
  	
  else 
    -- we are in standard time check mode to not run too fast 
    local timeUs = node.uptime() 
    if (timeUs - m._lastStepTime >= m._stepInterval) then
    	if (m._direction == m.DIRECTION_CW) then
  	    -- Clockwise
  	    m._currentPos = m._currentPos + 1
    	else
    	    -- Anticlockwise  
    	    m._currentPos = m._currentPos - 1
    	end
    	m.step(m._currentPos)
    
    	m._lastStepTime = timeUs -- Caution: does not account for costs in step()
    
    	return true
      
    else
      
    	return false
    	
    end
  
  end
  
end

-- @return long 
function m.distanceToGo()

    return m._targetPos - m._currentPos
end

-- @return long 
function m.targetPosition()

    return m._targetPos
end

-- @return long 
function m.currentPosition()

    return m._currentPos
end

-- Useful during initialisations or after initial positioning
-- Sets speed to 0
-- @param position long
-- @return nil 
function m.setCurrentPosition(position)

  m._targetPos = position
  m._currentPos = position
  m._n = 0
  m._stepInterval = 0
  m._speed = 0.0
end
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

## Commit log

2019-09-30 first check in
    [Actuator Circle.brd, Actuator Circle.sch, Bill of Materials.xlsx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]
2019-09-30 Update Bill of Materials.xlsx
    [Bill of Materials.xlsx]
2019-10-06 More readme content
    [Bill of Materials.xlsx]
2019-10-14 added acrylic balls
    [Bill of Materials.xlsx]
2019-10-29 BOM and Pick Place for SMT Assembly
    [Actuator Circle.csv, Bill of Materials.xlsx, JLCSMT_BOM1.xlsx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]
2019-11-27 Latest version
    [ESP32 Pin Mappings.xlsx]
